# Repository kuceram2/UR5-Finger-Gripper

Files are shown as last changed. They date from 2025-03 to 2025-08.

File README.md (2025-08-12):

# Universal Robots UR5 finger gripper

## Annotation
This thesis focuses on the design process of an open-source gripper for the UR5 collaborative
robot and other manipulators from Universal Robots. The design emphasizes easy integration
of the gripper into the robotic workspace, ensuring that the process is no more complex than
with commercial gripper models while also minimizing manufacturing complexity. The thesis
describes the design of the gripper body, which is produced using 3D printing, the electrical
wiring, the modules and components used for the gripper, and provides a detailed overview of
the software development aimed at facilitating the gripper's use with the robot. The work
includes a guide for manufacturing, assembly, connection to the robot, and commissioning of
the gripper. The appendices contain manufacturing documentation, including 3D models of
all parts, an electrical wiring diagram, a mechanical drawing, control software, and a test
program. The conclusion presents the functional product and describes the public release of
the project results as an open-source project.<br>
<b> Keywords </b> <br>
Gripper, robot, design, control, UR5, URCap

## Anotace
Tato práce se zabývá procesem návrhu open source chapače pro kolaborativní robot UR5 a další
manipulátory společnosti Universal Robots. V návrhu je kladen důraz na snadnou integraci
chapače do robotického pracoviště, aby proces nebyl složitější než u komerčních modelů
chapačů a zároveň na minimální náročnost výrobního procesu. Popisuje návrh těla chapače,
vyráběného pomocí 3D tisku, návrh elektrického zapojení, použitých modulů a komponet pro
chapač a podrobně i vývoj softwaru sloužícího pro snadné použití chapače s robotem. Práce
obsahuje návod na výrobu, sestavení, připojení k robotu a uvedení chapače do provozu.
Přílohami této práce jsou podklady pro výrobu, tedy 3D modely všech dílů, schéma
elektrického zapojení, mechanický výkres, ovládací software a zkušební program. V závěru je
představen funkční produkt a popsáno zveřejnění výsledků práce veřejnosti ve formátu open
source projektu.
<b> Klíčová slova </b> <br>
Chapač, robot, návrh, řízení

# DOKUMENTACE PRO KONSTRUKCI CHAPAČE
Tato část práce osahuje návod na sestavení, zprovoznění a základní způsob použití chapače s cobotem. Přílohou této práce je elektrické a mechanické schéma chapače. Mechanismus pohybu prstů chapače je převzatý z volně dostupné databáze 3D objektů Printables a jeho autorem je společnost A-11 Designs. Převzatý mechanismus jsem upravil v programu Fusion 360 za použití studentské licence a rozšířil ho o další části tak, aby splňoval nároky tohoto projektu. Rozšíření spočívalo ve vymodelování dílu pro uchycení krokového motoru a vnějšího krytu chránícího desku plošných spojů a vodiče. Vnější kryt zároveň umožnil spolehlivé upevnění chapače do příslušného rozhraní cobotu. Všechny zmíněné díly a součásti mechanismu prstů byly vyrobeny na 3D tiskárně z materiálu PET, ten jsem zvolil kvůli jeho lehkosti, pevnosti a dlouhodobé odolnosti. Výhodou této metody výroby dílů je možnost snadného a rychlého nahrazení poškozených nebo opotřebených součástí. Pro pevné spojení jednotlivých dílů jsou použity závitové vložky, zapuštěné přímo do dílů a šrouby. (13)
Proces konstrukce není časově náročný. Pokud pomineme čas, který vyžaduje 3D tisk součástek a vývoj desky plošných spojů, může být chapač sestaven, připojen k robotu a zprovozněn za 2 až 3 hodiny. O tom jsem se při sestavování prototypu sám přesvědčil. 
##	Výčet potřebných technologií a nástrojů
Jedním z cílů projektu je minimální náročnost konstrukce a maximální redukování potřebných technologií. Pro výrobu dílů těla chapače je použit 3D tisk, protože se v dnešní době čím dál více stává běžně dostupnou technologií. 3D tiskárnami je vybavena značná část středních odborných škol a gymnázií, ale i mnoho technologických firem a výrobních provozů. První prototyp byl vyroben na 3D tiskárně Prusa XL, ale malé rozměry dílů umožňují i využití tiskáren s menší pracovní plochou, jako jsou Prusa MK4 nebo Creality Ender-3. Za technologii výroby plošného spoje jsem zvolil ruční leptání desek s měděnou vrstvou. Tato jednoduchá technologie plně pokrývá nároky projektu a zbavuje potřeby využití služeb komerčního výrobce desek plošných spojů, což dále snižuje výsledné náklady na výrobu. Pro výrobu tak je potřeba pouze deska s vrstvou mědi a fotorezistu, maska pro leptání, která je přílohou práce, zdroj ultrafialového záření a vhodný leptací roztok, například chlorid železitý nebo persíran sodný. Pro osazení plošného spoje postačí vrtačka s vrtákem o průměru 0.5 mm, páječka a vhodná pájka, jelikož jsou použity výhradně THT  součástky. Dále už je potřeba pouze základní sada elektrikářských šroubováků a případně multimetr pro průběžnou kontrolu elektrického zapojení.
##	 Elektrické zapojení
Pro zprovoznění chapače je nejdříve potřeba správné zapojení elektronických součástek. K plošnému spoji, jehož výroba je popsána v předchozí kapitole, připájíme vodiče kabelu typu Lumberg RKMV 8-354 sloužícímu k napájení chapače a zároveň komunikaci s robotem podle schématu elektrického zapojení a této tabulky, která pro kontrolu obsahuje i umístění vodičů v konektoru. Schéma elektrického zapojení je přílohou této práce. (5)
<table>
Barva vodiče	Číslo pinu	Signál
Červená	8	0V(GND)
Šedá	5	0V/+12V/+24V (PWR)
Modrá	7	Digitální výstup 8 (DO8)
Růžová	6	Digitální výstup 9 (DO9)
Žlutá	4	Digitální vstup 8 (DI8)
Zelená	3	Digitální vstup 9 (DI9)
Bílá	1	Analogový vstup 2 (AI2)
Hnědá	2	Analogový vstup 3 (AI3)
</table>

Obrázek 12 - Schéma konektoru nástroje, převzato z https://community.particle.io/t/tracker-one-analog-sensor-reading-and-publishing/65011
K určeným pinům řadiče připojíme vinutí krokového motoru. Při zapojování dbáme, aby byly oba konce jednoho vinutí připojeny k sousedním pinům a nikoli střídavě. Je důležité nikdy nepřipojovat ani neodpojovat krokový motor, když je řadič pod napětím, jinak dojde k nevratnému poškození řadiče a bude potřeba ho vyměnit.
Pokud zamýšlíme používat chapač v dlouhých souvislých časových úsecích, je žádoucí přidat na čip řadiče pasivní chladič, protože při provozu delším, než několik minut vzroste teplota čipu a tím negativně ovlivní přesnost řízení motoru. K volným pinům DI8 a PWR připojíme kontakty koncového spínače umístěného na jedné z kontaktních plošek chapače, ten slouží pro detekci kontaktu s manipulovaným předmětem a pro kalibraci.

Obrázek 13 - Připojení krokového motoru, vytvořeno autorem
4.3	 Sestavení chapače
Pro sestavení chapače jsou potřeba součástky uvedené v následující tabulce v odpovídajícím množství. Přílohou této práce jsou modely všech dílů ve formátu STL, sloužící jako podklady pro 3D tisk. Vhodným materiálem pro výrobu je PLA nebo PETG. Použitému materiálu je potřeba přizpůsobit teplotu páječky při osazování závitových vložek a matice pro trapézovou tyč.

Tabulka 5 – Kusovník, vytvořeno autorem
Součástka	Množství, (popis)	Součástka	Množství, (popis)
 	1x
válcový kryt	 	1x
základní díl prstů
 	1x
zadní kryt	 	1x
držák krokového motoru
 	1x
středový díl	
 	4x
dlouhé táhlo
 	2x
prst chapače	 	4x
krátké táhlo
 	2x
středové táhlo	Krokový motor NEMA 17 17HS3401	1x
krokový motor
Šroub M5x15	8x	Šroub M4x20	4x
Šroub M8x10	4x	Šroub M5x10 samořezný	6x
Matice M5	8x	Matice M4	4x
Závitová vložka M5	8x	Trapézová závitová tyč M8	1x
Šroub M5x20	8x	Matice na závitovou tyč M8	1x
Šroub M3x5	4x	Hřídelová spojka M8	1x

Všechny obrázky použité v tabulce výše jsou autorské a byly pořízeny v programu Fusion 360 používaném ve studentské licenci.
Dle obrázku zapustíme do vyznačených otvorů vložky. Je potřeba vložky nahřát páječkou, zatlačit do otvoru a nechat vychladnout.

Dle obrázku přišroubujeme krokový motor čtyřmi šrouby M3x5 k držáku. Na osu krokového motoru připevníme hřídelovou spojku M8.

Dle obrázku přišroubujeme základní díl prstů čtyřmi šrouby M5x15.

K hřídelové spojce připevníme trapézovou tyč. Dle obrázku přišroubujeme válcový kryt čtyřmi šrouby M5x15. Ke krokovému motoru připojíme vodiče.

Dle obrázku sestavíme mechanismus prstů chapače. Do středového dílu po nahřátí páječkou vložíme matici M8. Pro červeně označené otvory použijeme 8 šroubů M5x20, pro modře označené otvory použijeme 4 šrouby M4x20 a odpovídající počet příslušných matic. 
Obrázek 18 - Sestavení, krok 5, foto: autor

K patici nástroje na cobotu přišroubujeme čtyřmi šrouby M8x10 zadní kryt chapače.
 
Obrázek 19 - Sestavení, krok 6, foto: autor

Připojíme plošný spoj ke krokovému motoru podle schématu elektrického zapojení a vložíme ho dovnitř chapače. Vyvedeme příslušným otvorem signální kabel z plošného spoje ven z těla chapače. Dle obrázku přišroubujeme zadní kryt chapače šesti šrouby M5x10. Tímto je chapač sestaven a připraven k použití.
 
Obrázek 20 - Sestavení, krok 7, foto: autor
Sestavený chapač je 235 mm dlouhý, tělo je v nejširším bodě široké 103 mm a maximální efektivní rozevření kontaktních ploch je 120 mm.

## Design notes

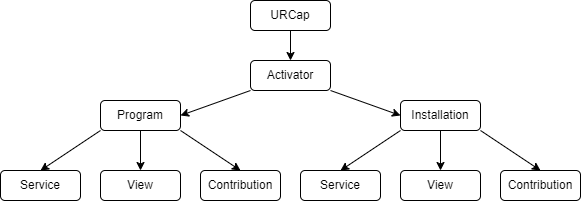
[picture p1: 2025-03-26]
schémata/URCap structure.png

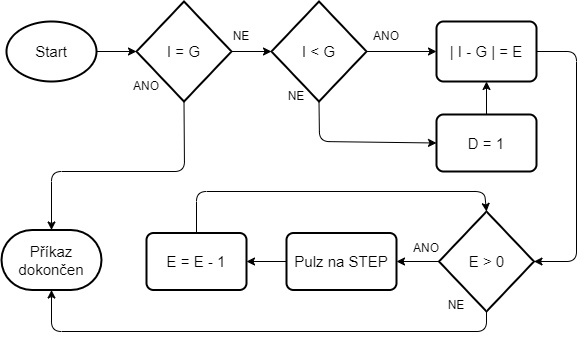
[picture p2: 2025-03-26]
schémata/gripper_vyvojovy_diagram.png

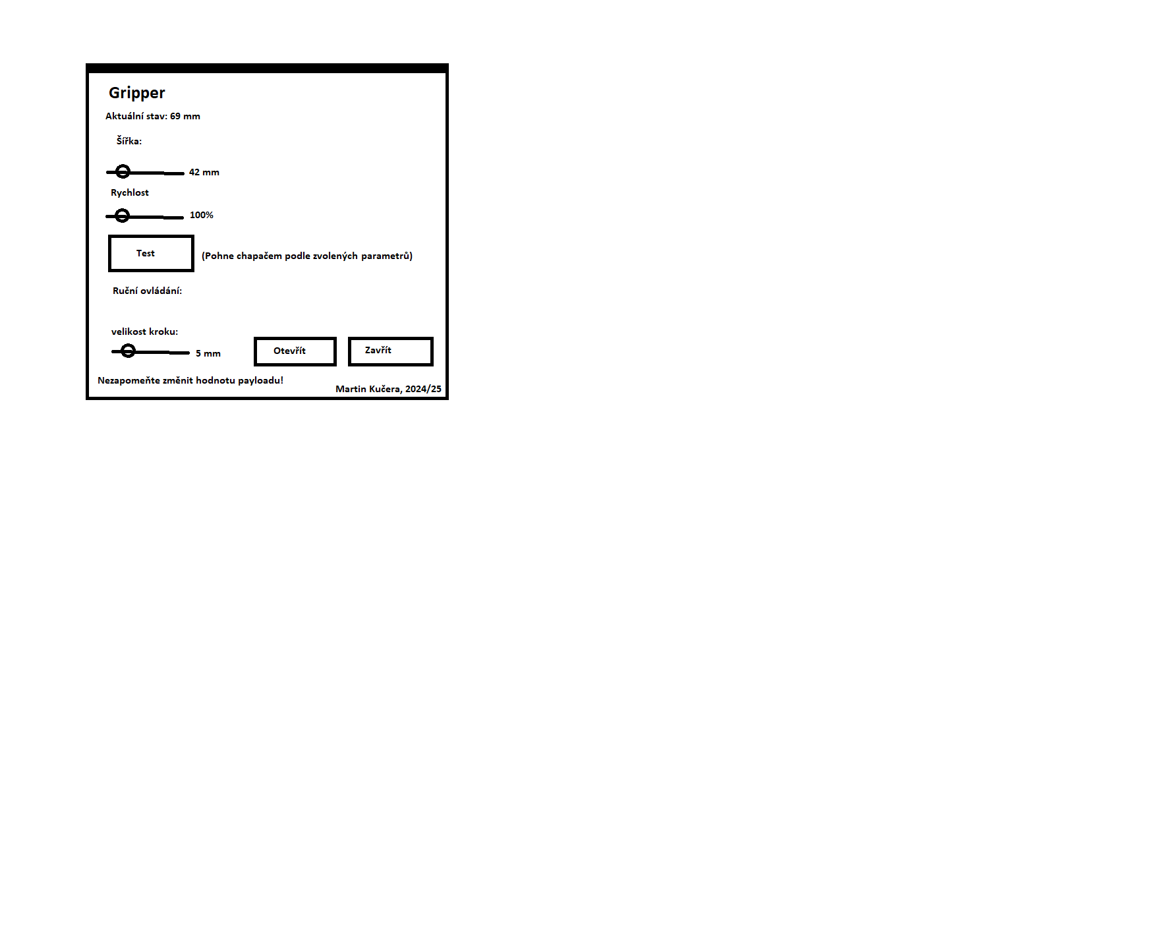
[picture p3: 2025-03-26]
schémata/URCap sketch.png

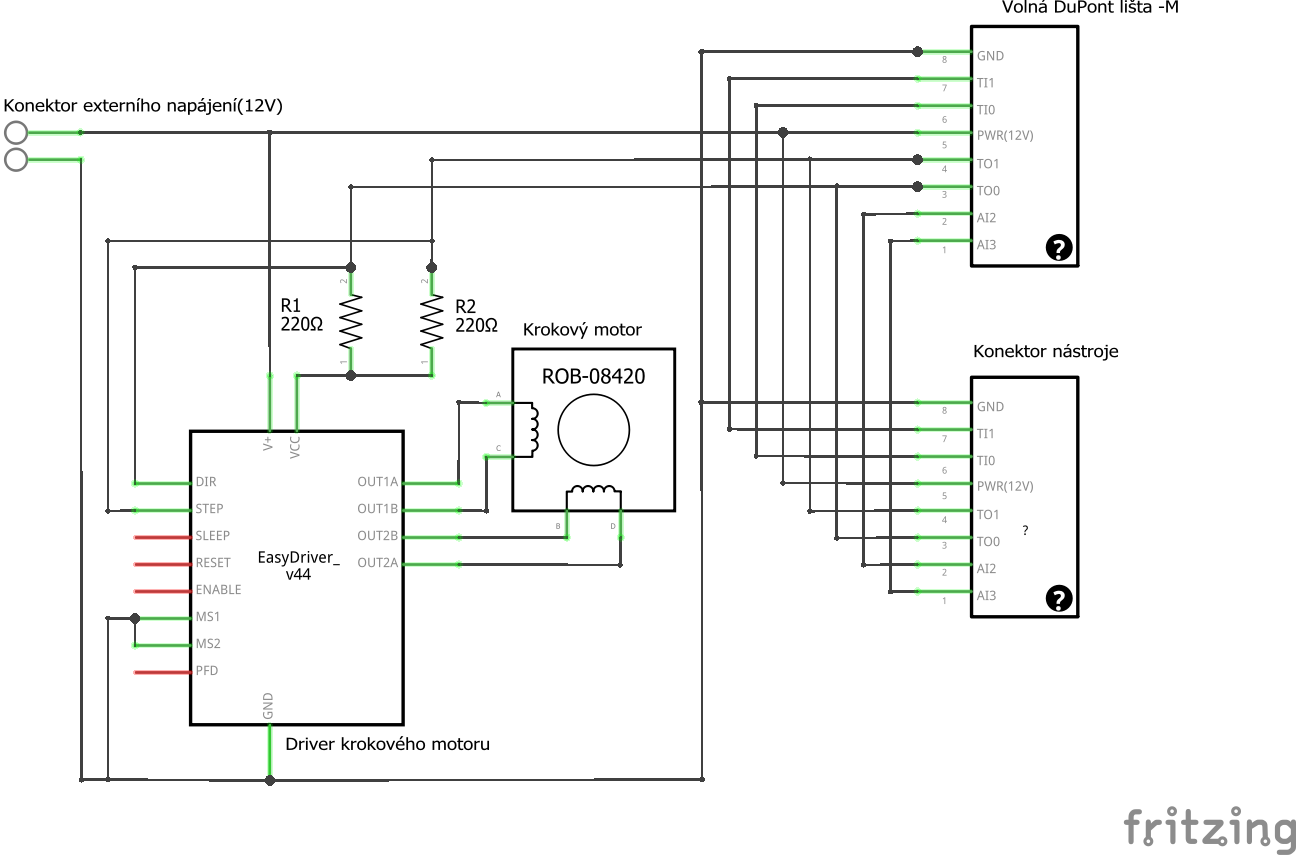
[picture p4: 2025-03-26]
schémata/elektro schéma_schem.png

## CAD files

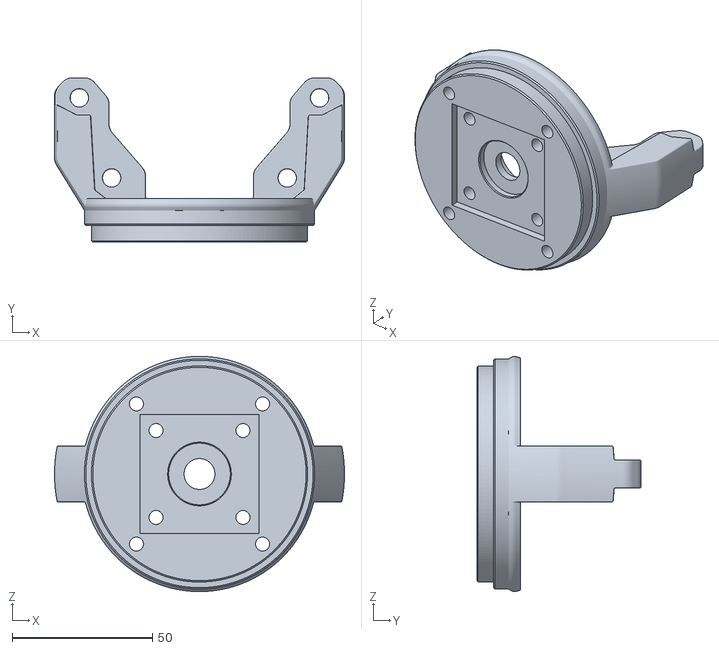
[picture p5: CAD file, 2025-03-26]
podklady/3D modely/základní díl prstů.stl
103.4 x 58.7 x 83.9

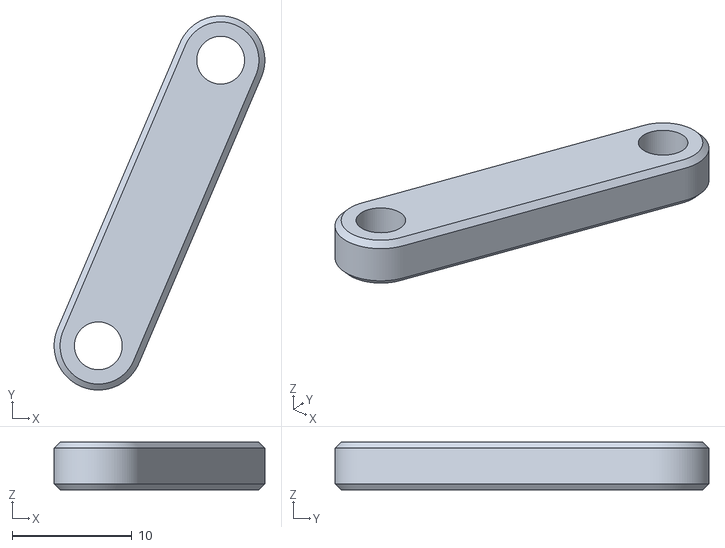
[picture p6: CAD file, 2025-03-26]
podklady/3D modely/středové táhlo.stl
17.6 x 31.3 x 4.00

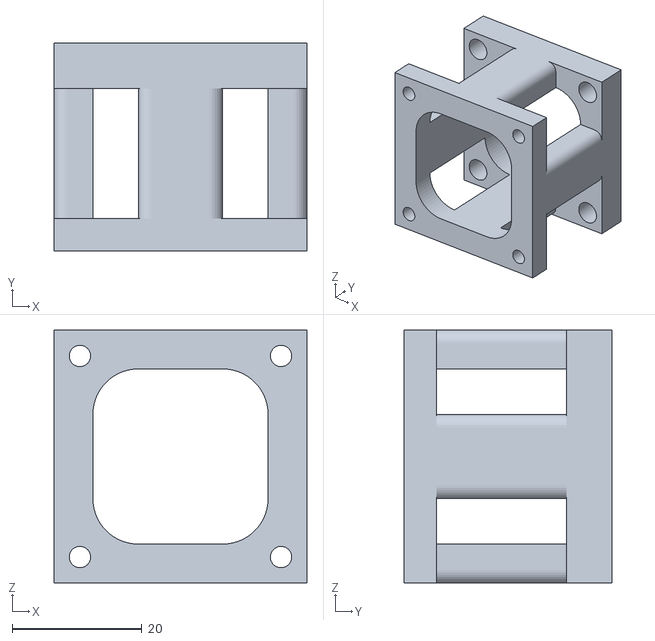
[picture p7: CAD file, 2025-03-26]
podklady/3D modely/držák krokového motoru.stl
39.0 x 32.0 x 39.0

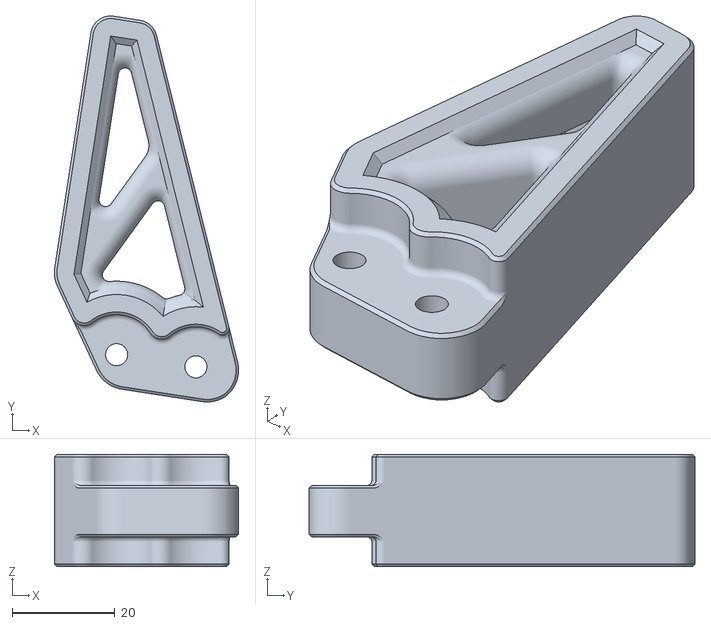
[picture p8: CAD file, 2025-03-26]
podklady/3D modely/prst chapače.stl
35.8 x 75.1 x 21.8

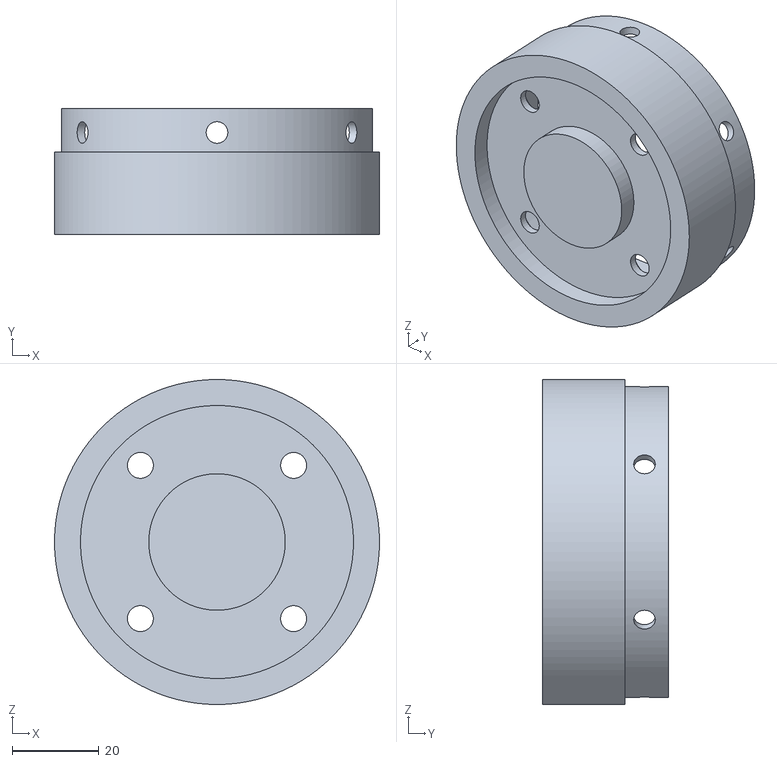
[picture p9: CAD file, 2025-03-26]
podklady/3D modely/zadní kryt.stl
75.0 x 29.0 x 75.0

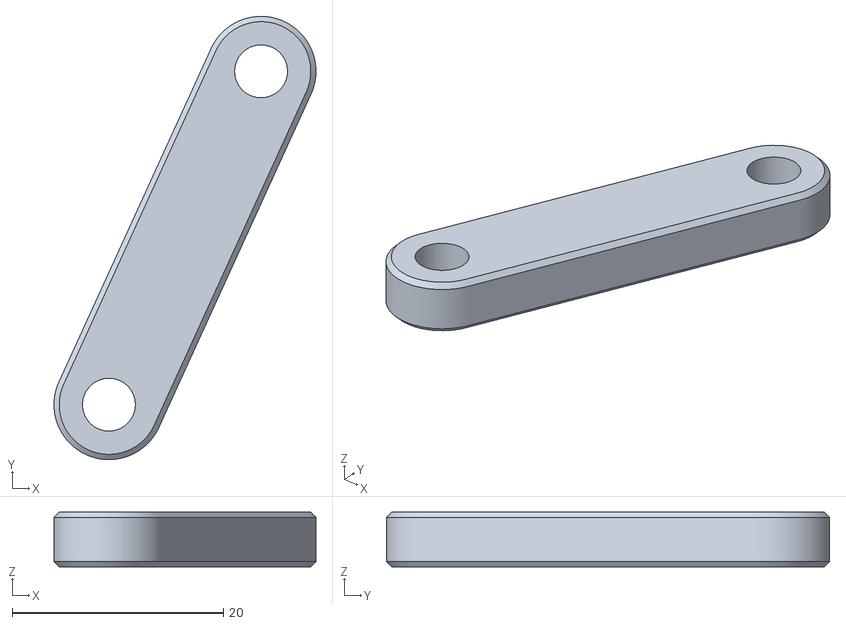
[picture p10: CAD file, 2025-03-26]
podklady/3D modely/krátké táhlo.stl
24.8 x 41.9 x 5.20

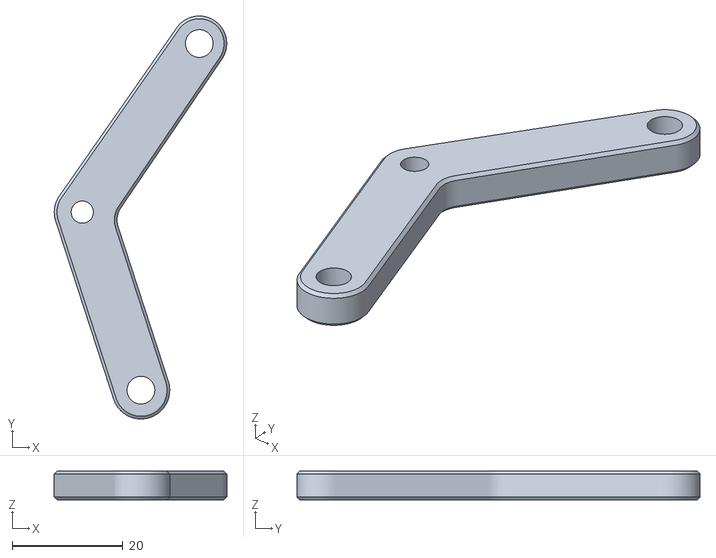
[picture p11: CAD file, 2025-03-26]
podklady/3D modely/dlouhé táhlo.stl
31.1 x 72.7 x 5.20

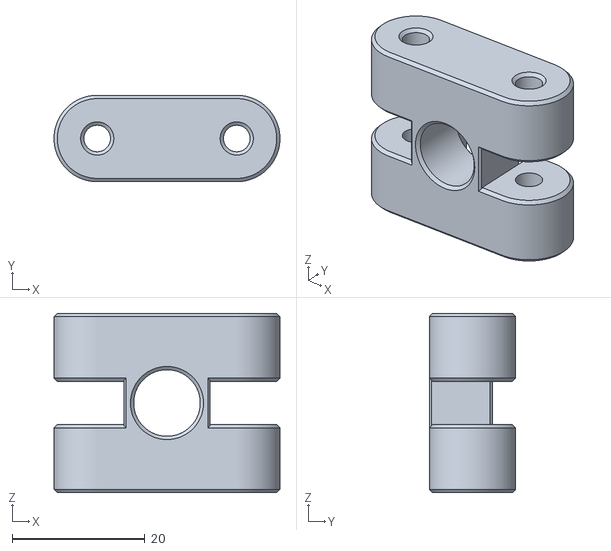
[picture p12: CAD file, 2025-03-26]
podklady/3D modely/středový díl.stl
34.0 x 13.0 x 27.0

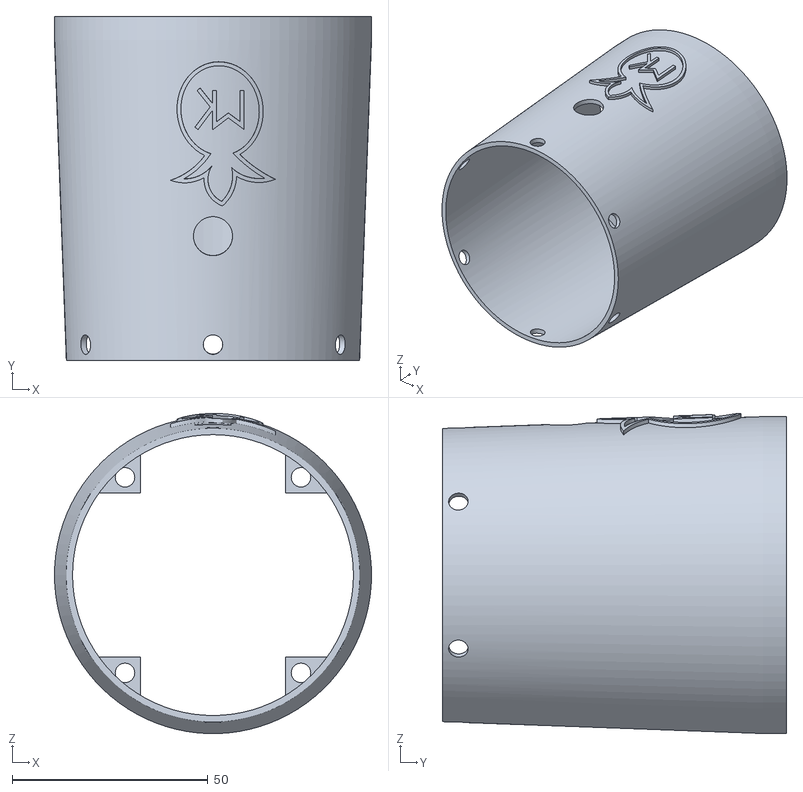
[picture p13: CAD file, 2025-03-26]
podklady/3D modely/válcový kryt.stl
81.1 x 87.9 x 81.8

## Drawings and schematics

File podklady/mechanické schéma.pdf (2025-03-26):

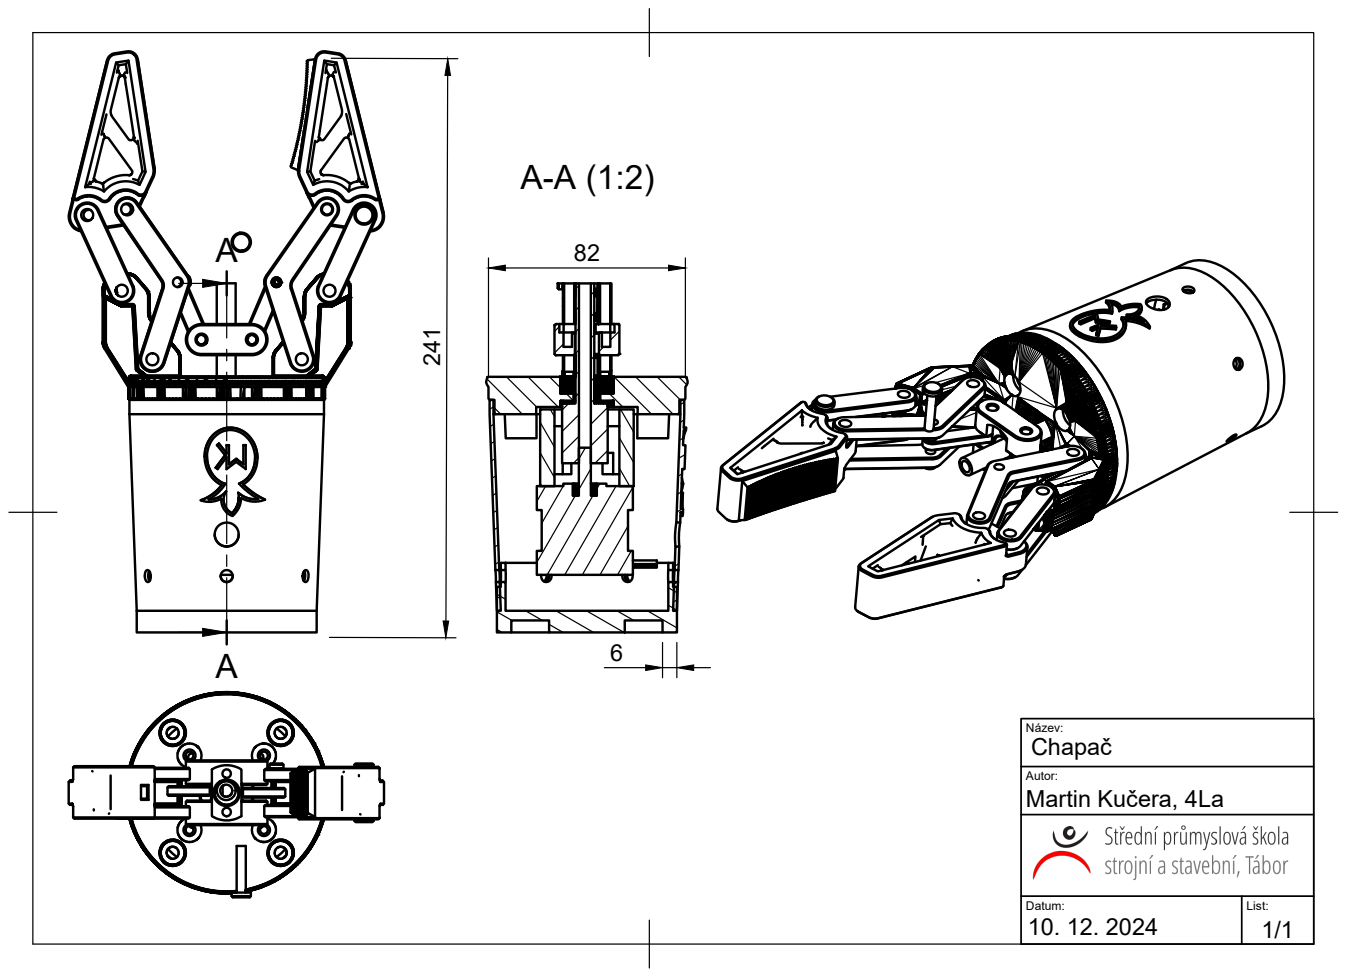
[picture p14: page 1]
Martin Kučera, 4La

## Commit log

2025-03-26 přidány podklady
    [dlouhé táhlo.stl, držák krokového motoru.stl, krátké táhlo.stl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]
2025-03-26 updated podklady
    [dlouhé táhlo.stl, držák krokového motoru.stl, krátké táhlo.stl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]
2025-03-26 added schematics
